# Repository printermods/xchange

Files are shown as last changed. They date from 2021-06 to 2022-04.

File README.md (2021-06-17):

# XChange
XChange printable adapters, firmware, knowledge base, accessories
(This repository will be updated frequently as we further develop adapters, installation and operation support materials, and more. Please contact us directly for general one-on-one help at support@printermods.com)

======================================================

# Start Here
Read and watch the following before beginning installation of your XChange:

#1 - XChange V1.0 - Basic Installation Instructions: https://www.youtube.com/watch?v=RV0KnSQEELk

#2 - Warnings and Pre-Installation Checklist: https://github.com/printermods/xchange/blob/main/XChange%20V1.0%20-%20Pre-Installation%20Checklist%20Rev%200.pdf

#3 - Wiring Notes and Diagrams: https://github.com/printermods/xchange/blob/main/XChange%20V1.0%20-%20Wiring%20Diagrams.pdf

#4 - Measuring and Calculating Belt Length: https://github.com/printermods/xchange/blob/main/XChange%20V1.0%20-%20Belt%20Lengths.pdf

#5 - Frequently Asked Questions: https://github.com/printermods/xchange/blob/main/FAQ

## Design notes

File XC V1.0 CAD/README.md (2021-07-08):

As we release CAD files for XChange, they will be organized and updated here.

*All works herein published under the Creative Commons Attribution-NonCommercial 4.0 International license: https://github.com/printermods/xchange/blob/main/LICENSE.txt *

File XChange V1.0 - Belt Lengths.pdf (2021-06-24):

# XChange V1.0 - Belt Lengths

## How to Determine if You Need a Different Belt

You may need to replace your X axis drive belt in order to use XChange on your 3D printer, if the belt tabs on XChange are significantly longer or shorter than the ones currently in use on your machine.

Below is a chart of the belts that we’ve personally tested on some popular machines. Note that lengths in this chart represent the belt length between the ferrules (terminations). We’ll update it as we confirm new lengths, and receive input from you!

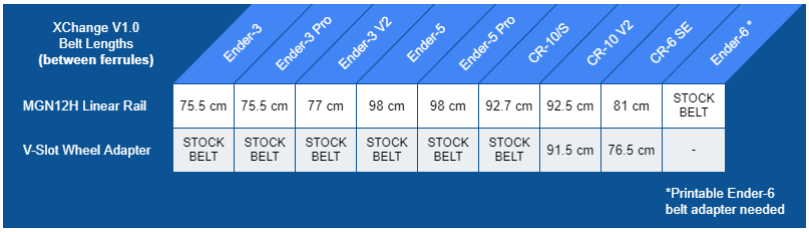
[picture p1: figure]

Measuring Custom Belt Length
If you don’t see your printer listed above, don’t worry, there are a couple of options. The simplest is to just install XChange, and cut a piece of belt to the appropriate length. You can terminate the ends by folding the end of the belt over itself to make a loop, then securely fastening with zip ties:

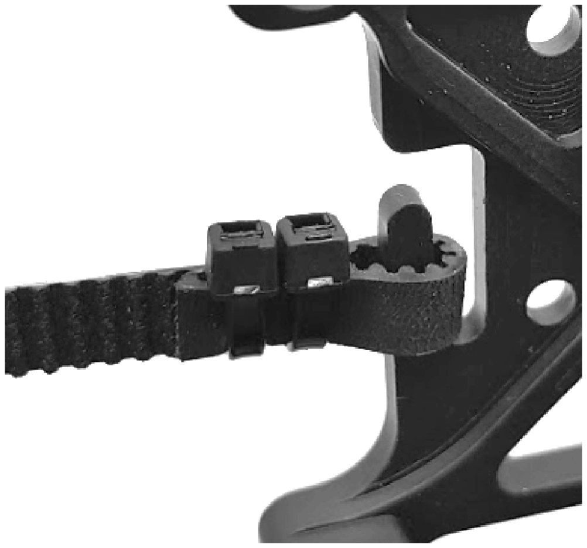
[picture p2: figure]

## XChange V1.0 - Belt Lengths

Belt Length Calculator
You can alternatively use our spreadsheet to measure and calculate the specific length you’ll need for your installation, depending on your X axis linear motion. If you provide this information to us at the time of placing your order, we can custom cut and pre-terminate a high quality belt for you.

Note: Belt length calculator spreadsheet is downloadable, and .XLSX format. You can upload to and open in a free Google Drive account if you don’t have Microsoft Excel:

https://drive.google.com/file/d/1cvCTFK-Esp-tSwJrwVX8-UBtqmJn4-DE/view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 (https://drive.google.com/file/d/1cvCTFK-Esp-tSwJrwVX8-UBtqmJn4-DE/view)

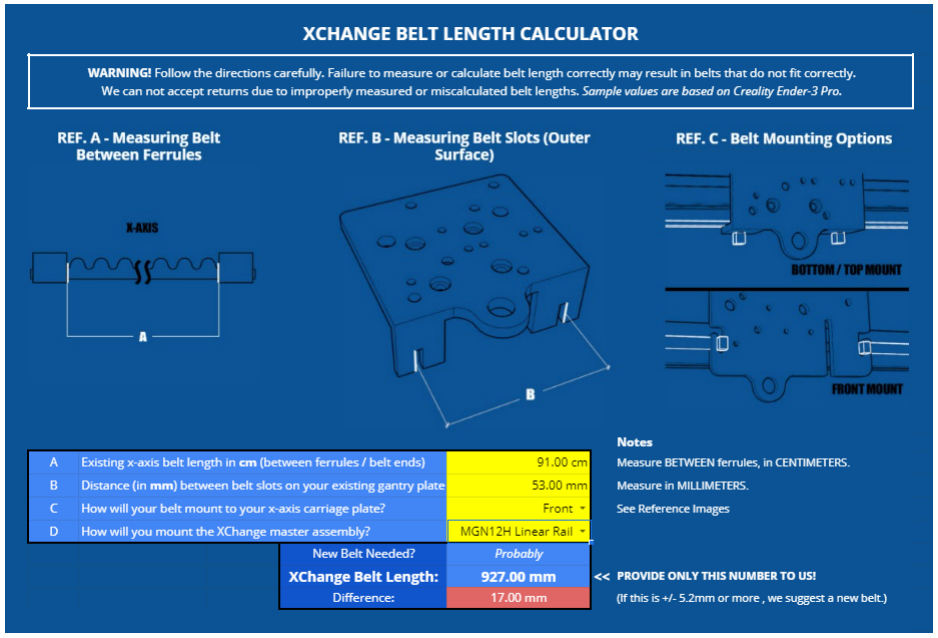
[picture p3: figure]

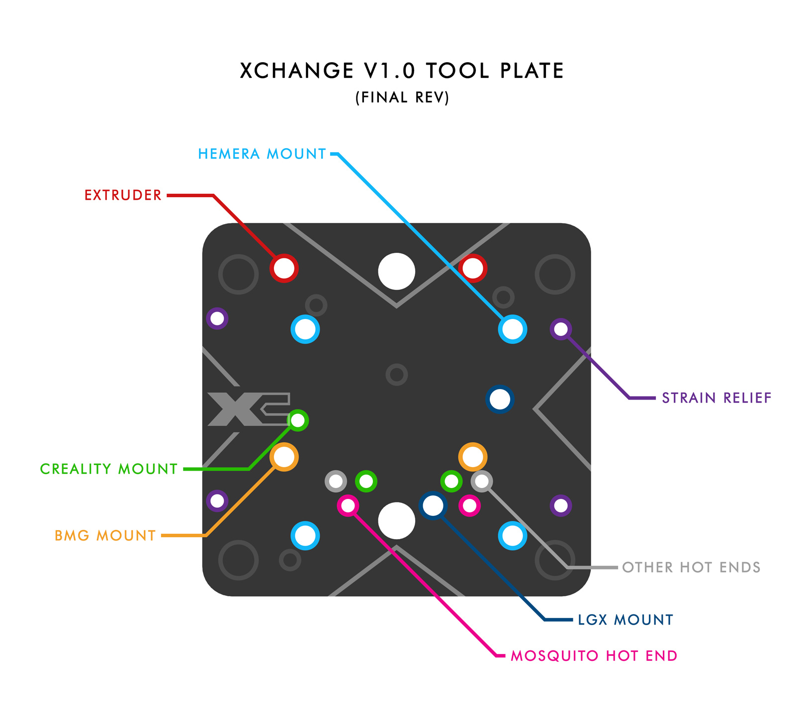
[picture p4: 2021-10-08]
XChange-v1-tool-plate-diagram.jpg

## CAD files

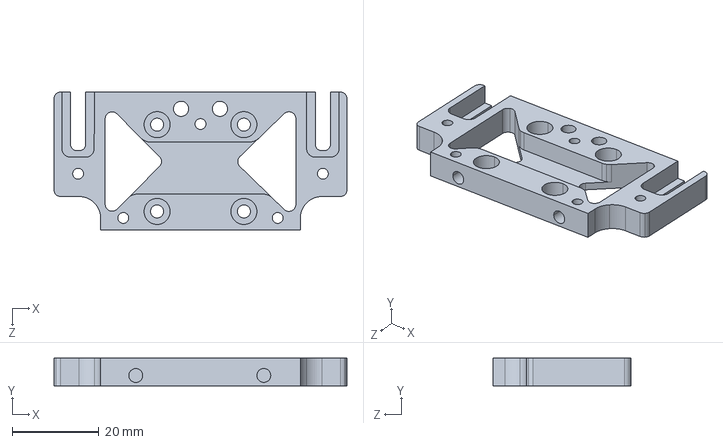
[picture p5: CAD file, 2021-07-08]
XC V1.0 CAD/STEP/Master-Assembly-M2-V9.step
67.5 x 6.35 x 31.8 mm

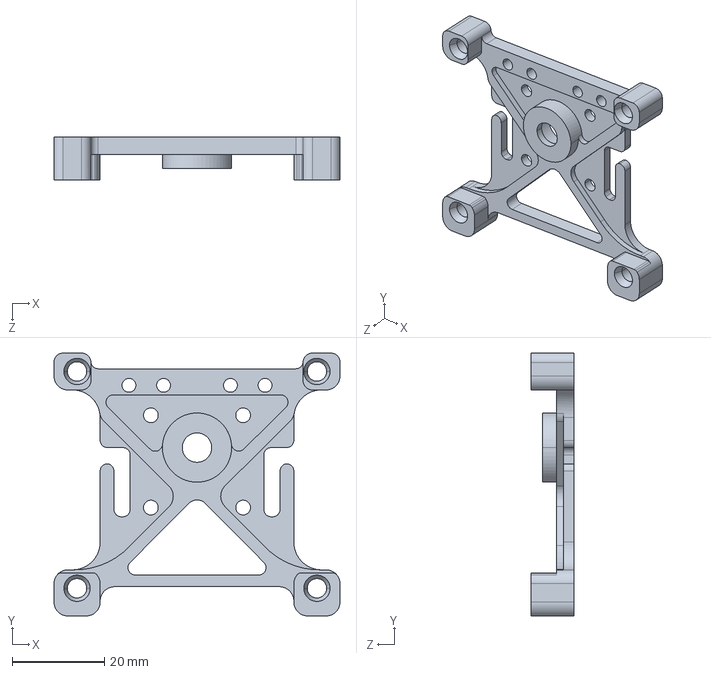
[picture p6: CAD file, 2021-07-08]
XC V1.0 CAD/STEP/Master-Assembly-M1-V13.step
62.0 x 57.0 x 9.30 mm

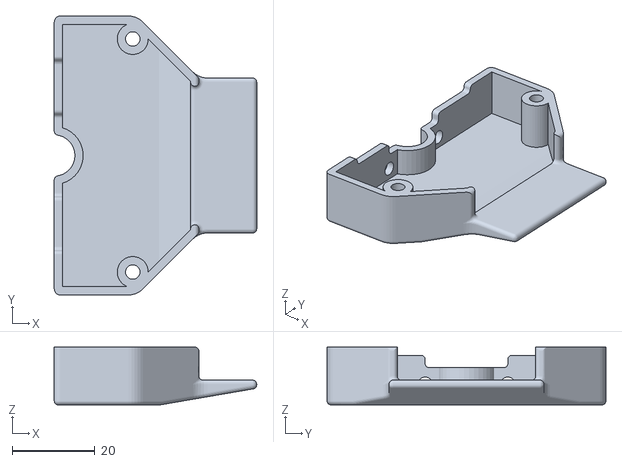
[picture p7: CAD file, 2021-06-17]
Printable Files/Master Assembly Cover - TT.stl
49.0 x 67.5 x 14.0

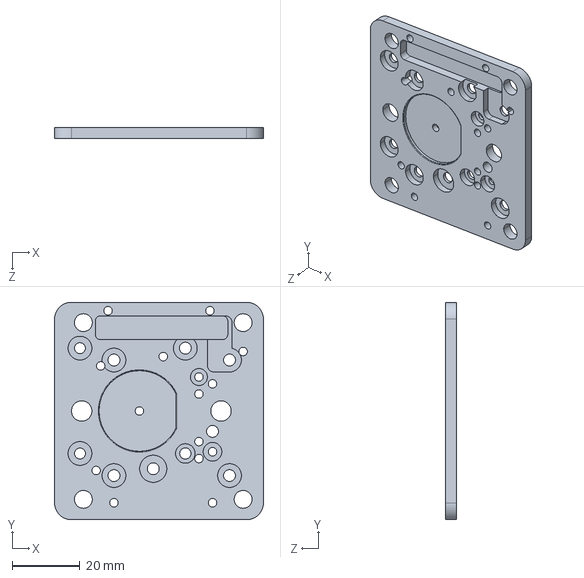
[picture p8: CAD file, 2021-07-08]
XC V1.0 CAD/STEP/Tool-Assembly-Plate-V2.step
61.5 x 64.0 x 3.18 mm

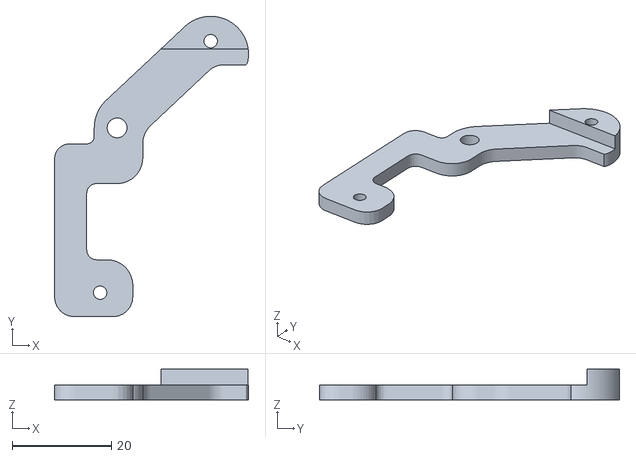
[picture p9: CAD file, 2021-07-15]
Printable Files/ender-stock-fan-shroud-xchange-v2.stl
39.1 x 60.6 x 6.18

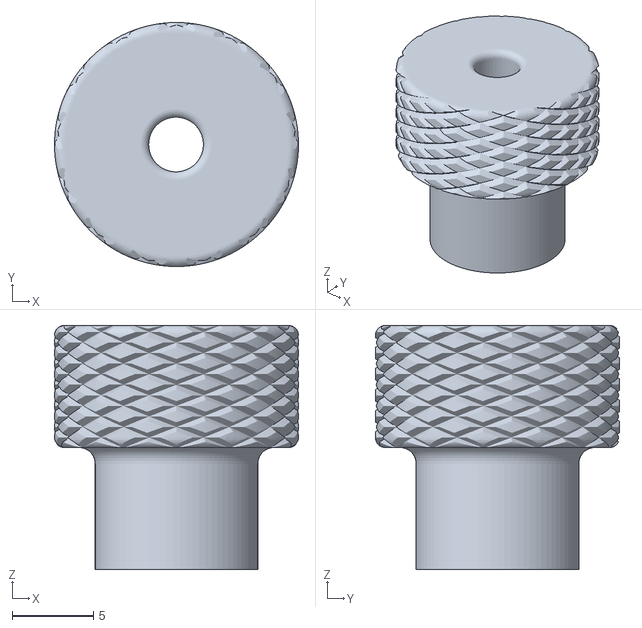
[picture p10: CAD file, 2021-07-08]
Printable Files/alignment-tool-v2.stl
15.0 x 15.0 x 15.0

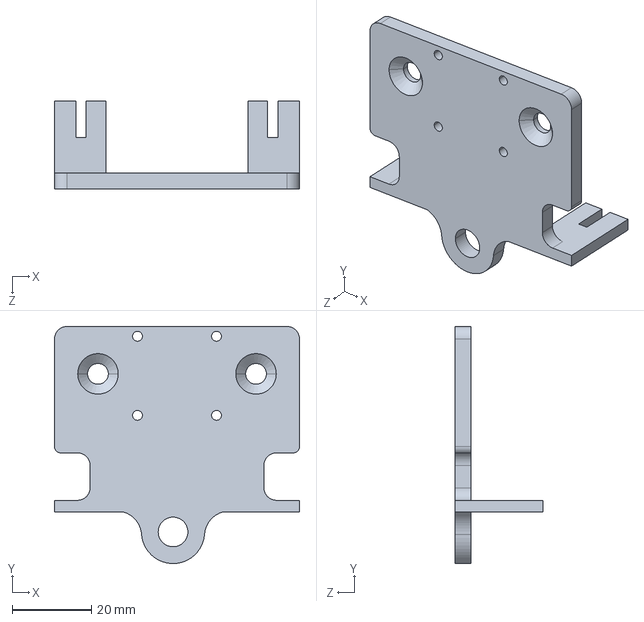
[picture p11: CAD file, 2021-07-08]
XC V1.0 CAD/STEP/E3-V-Slot-Adapter.step
62.0 x 60.0 x 22.2 mm

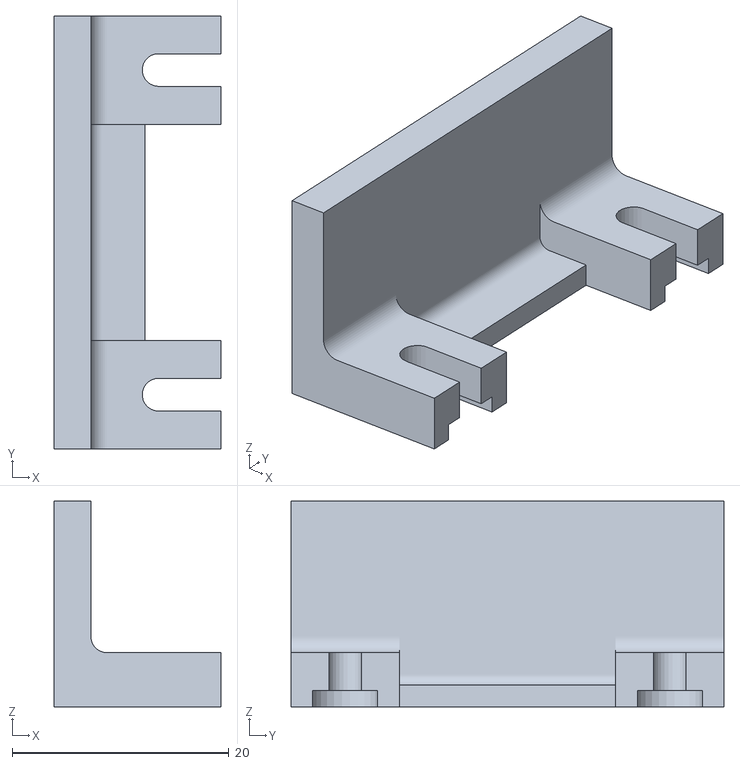
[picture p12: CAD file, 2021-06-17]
Printable Files/tool-plate-wire-cover.stl
15.4 x 40.0 x 19.0

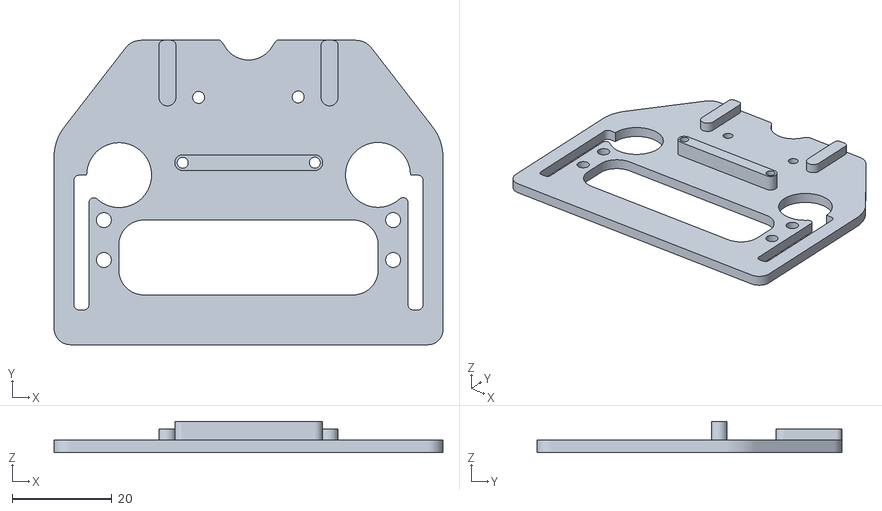
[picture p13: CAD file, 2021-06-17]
Printable Files/Ender 6 Printable Belt Adapter v4.stl
78.0 x 61.1 x 6.30

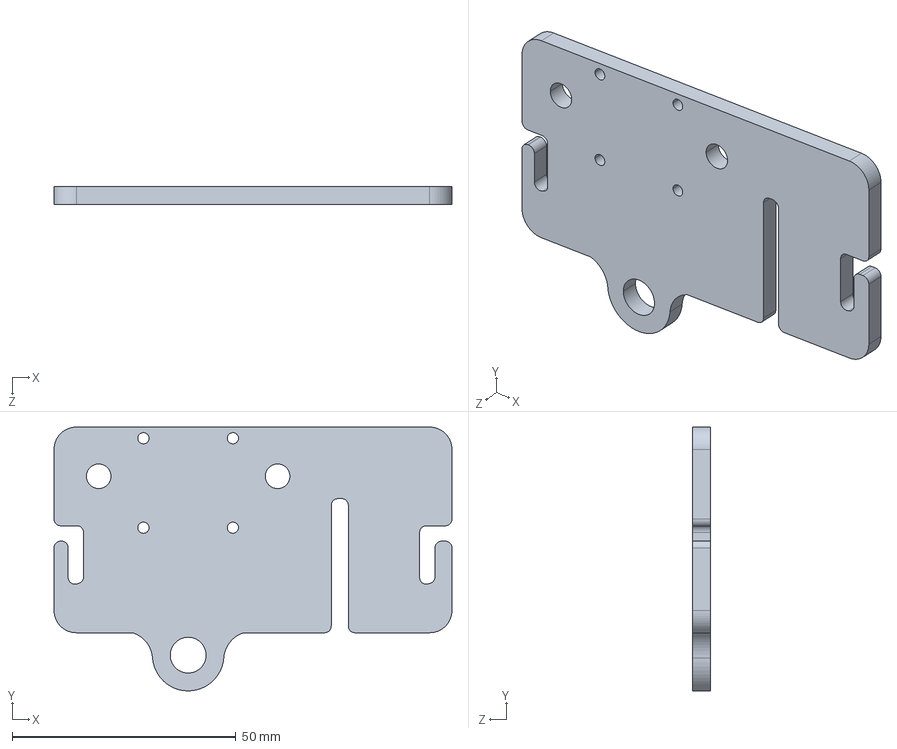
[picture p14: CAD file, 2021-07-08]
XC V1.0 CAD/STEP/E5-V-Slot-Adapter.step
89.0 x 59.0 x 4.00 mm

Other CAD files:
XC V1.0 CAD/STL/M2-v9.stl
XC V1.0 CAD/STL/M1-v13.stl
XC V1.0 CAD/STL/E3-V-Slot-Adapter.stl
XC V1.0 CAD/STL/E5-V-Slot-Adapter.stl
XC V1.0 CAD/STL/Tool-Assembly-Plate-V2.stl

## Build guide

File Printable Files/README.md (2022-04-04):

**Have a print you'd like us to share? Send it to us, along with a description, at support@printermods.com and we'll check it out!**

**Alignment Pin Tightening Tool:**
https://github.com/printermods/xchange/blob/main/Printable%20Files/alignment-tool-v2.stl

**Ender-6 Printable CoreXY Belt Adapter:**
https://github.com/printermods/xchange/blob/main/Printable%20Files/Ender%206%20Printable%20Belt%20Adapter%20v4.stl  

**Ender-3 / Ender-5 / CR-10 Style Fan Cover Adapter:**
https://github.com/printermods/xchange/blob/main/Printable%20Files/ender-stock-fan-shroud-xchange-v2.stl

**Tool Plate Wire Cover:**
https://github.com/printermods/xchange/blob/main/Printable%20Files/tool-plate-wire-cover.stl  

**Master Assembly Cover (90º wire strain relief)**
https://github.com/printermods/xchange/blob/main/Printable%20Files/Master%20Assembly%20Cover%20-%20TT.stl  
*Design credit: Teaching Tech*

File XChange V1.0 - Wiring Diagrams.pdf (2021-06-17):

# XChange V1.0 - Wiring Notes and Diagrams

## Wiring XChange Master and Tool Assemblies

Wiring your Master and Tool Assemblies is actually quite simple, and wiring is 1:1 between the Master PCB and Tool PCBs. This means that whatever circuit you wire to the “HF+” connector on the Master PCB will correspond exactly to the “HF+” connector on the tool PCB.

ONLY wire your heater cartridge to the connections labeled “+” and “-”, as these are connections with thicker board traces specifically for higher wattage components.

For installations requiring a more advanced understanding of XChange’s circuit paths, please refer to the schematics at the end of this document.

## XChange V1.0 - PCB Wiring Diagrams

Master PCB Drawing

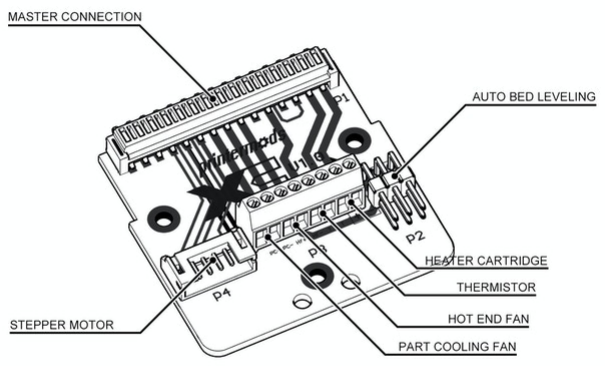
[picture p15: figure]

## XChange V1.0 - PCB Wiring Diagrams

Tool PCB Drawing

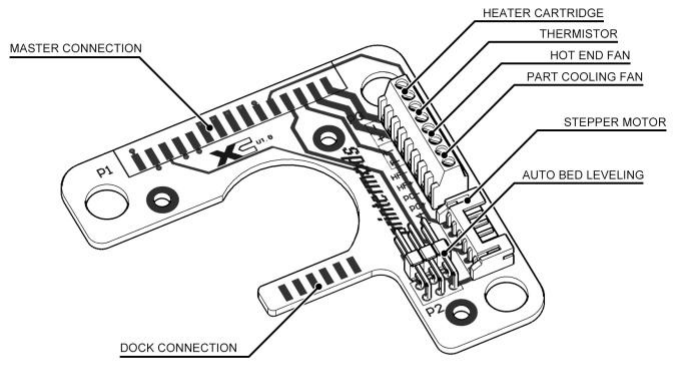
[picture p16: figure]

## XChange V1.0 - PCB Wiring Diagrams

### (MASTER PCB SCHEMATIC)

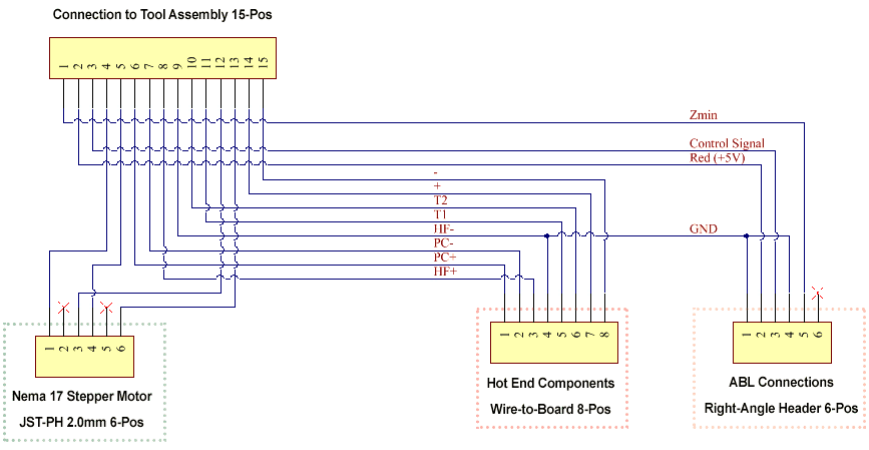
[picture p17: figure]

## XChange V1.0 - PCB Wiring Diagrams

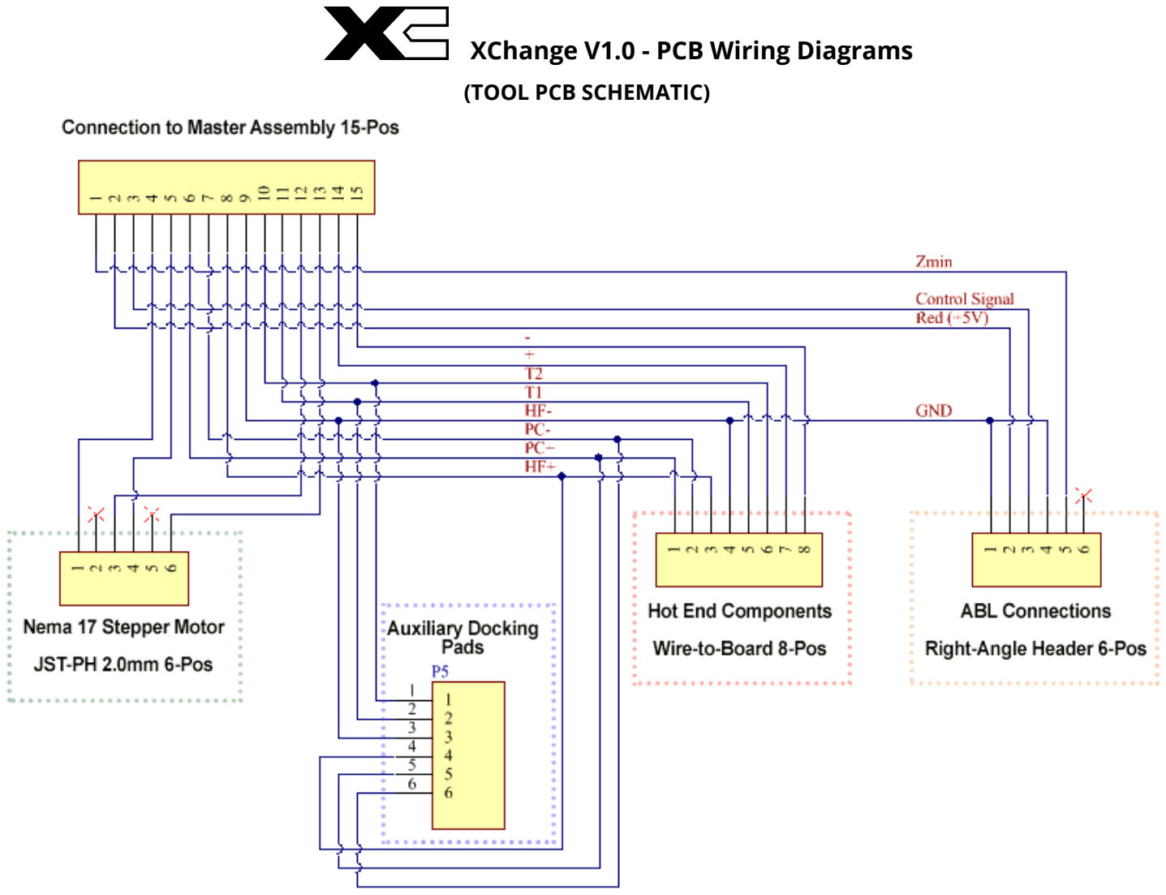
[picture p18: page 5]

### (TOOL PCB SCHEMATIC)

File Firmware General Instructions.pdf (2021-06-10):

The most current firmware solution for XChange is Marlin-bugfix-2.0.x, which has had revisions made by a Marlin firmware dev now merged into the official branch. The primary change is the ability to define M206 offsets while using Marlin’s tool change functionality.

Tool presets are stored on the “auto0.g” file, which should be loaded to the printer’s SD card (card should be inserted prior to powering the printer on).

The format for tool head configuration in auto0.g is as follows:

M810 M206 X0Y0Z0 | M92 E93 | M301 P21.3I1.54D76.55 | M204 P500 R500 T500
| M900 K0.0 | M305 R4700 T100000 B4092; Stock Head

M81X - Tool number
M206 - Toolhead offset relative to zero
M92 - E-step calibration
M301 - PID calibration
M204 - Acceleration values
M900 - Linear Advance settings
M305 - Thermistor parameters

Please exercise caution when using this experimental firmware and tool changing configuration files. Be especially careful when attempting bed leveling, and ensure that Z safe homing is enabled. It is recommended to use only manual mesh bed leveling with XChange for now.

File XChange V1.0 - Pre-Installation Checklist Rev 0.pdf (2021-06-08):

# XChange V1.0 - Pre-Installation Checklist

# WARNING!

This device is not a toy. If you are not knowledgeable about 3D printer electronics, please consult an electrical professional for help with installation. Always service your XChange-equipped 3D printer with the power OFF, as its magnets are capable of attracting metallic tools and objects with significant force. The magnetic locking system poses a pinching hazard, and may cause injury if misused. If misused or installed incorrectly, or used without supervision, this device may damage your 3D printer and other electronics. We are not liable for damage arising from the use or misuse of this device.

## Before you begin…

XChange is the first system of its kind, and you are one of the first with access to it! While this system was generally designed for compatibility with most 3D printers, there are MANY variables that impact compatibility with different machines and accessories. Before converting your machine to use XChange, it’s important that you take your time, think carefully about all the steps, and print or purchase anything you’ll need that you don’t already have. Please watch any and all instructional videos ahead of time to understand any hurdles you may encounter.

We’ll be working to ensure compatibility for as many machines as we can, and this process will be heavily dependent on design input and contributions made by the community. We appreciate your patience during this process, and ask that you refer to github.com/printermods/xchange to find helpful documentation, files, and share with the community.

## 1. Plan your build!

”Measure twice and cut once.” Gather all printable files you’ll need, and identify any parts you’ll need to design, find or purchase. Think about belts, endstops, coordinate changes, firmware adjustments, etc. Then, start by getting your machine printing perfectly with a single tool before moving to assembling the next one. Use our support channels and growing knowledge base for answers to your general installation and usage questions.

Find our downloads and knowledge base at github.com/printermods/xchange

2. Use support resources (and contribute, if you’d like).
XChange’s Kickstarter campaign has granted backers early access to pre-release offerings.

XChange V1.0 Pre-Installation Checklist - Rev. 0

As XChange has not yet been commercially released, it may require adaptation to suit your specific printer model-- adaptation that we may or may not yet have developed or vetted. The feedback and ideas you provide helps us make XChange even better and broadly compatible as we move forward. Be sure to check all documentation, warnings, and requirements before installing XChange.

3. Be careful.
We recommend installing XChange on secondary or non-critical machines until you are completely familiar with its installation, maintenance, and usage. You can avoid costly mistakes by following common sense guidelines such as:
- Print the appropriate master assembly strain relief adapter, and ensure all connections have proper strain relief.
- Print and attach the master assembly safety shroud (never use XChange without this part in place).
- Only service your machine with the power OFF.
- Never place your fingers or any other objects between the magnetic assemblies.
- The magnets are strong enough to grab tools such as screwdriver and hex key bits, so use caution when working in close proximity to them.
- Take care to correctly align tool plates as they are attached to the master assembly.
- Do not drop tool assembly, as pins can break and components may be damaged.
- Take care to leave no stray wires when inserting stripped ends into wire-to-board connectors.
- Additional mechanical reinforcement may be necessary when using tool plate accessories in excess of 600g.
- Do not exceed the rated safe electrical limitations of the PCBs of 2.8A per pin.

## 4. Have fun!

Perhaps most importantly, we hope XChange sparks new ideas and creative ways for you to use your 3D printer. We’d really love to hear from you, and encourage you to share your successes— and failures— with us. Our team has worked tirelessly to provide you something we hope you’ll really love, and sharing those experiences with us is very meaningful to everyone. Reach out to us directly at support@printermods.com .

We sincerely thank you for being our backer, and making XChange possible. <3

XChange V1.0 Pre-Installation Checklist - Rev. 0

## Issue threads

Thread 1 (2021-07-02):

Couple questions

zcohenld, 2021-07-02:
I received my XChange today and have been playing with it a bit. Haven't mounted anything yet since I'm still figuring out how I'm going to do everything. A few things have come up though that I wanted to ask/bring up for others.

- The installation guide video needs some work. The sound is pretty bad and sometimes its hard to see whats actually being done. I dont expect it any time soon, but I feel videos in general just aren't the best way to show how to assemble something. I found the [Inventables X-Carve instructions](https://x-carve-instructions.inventables.com/1000mm/) to be extremely well done. Something like that would be really helpful.
- It would be helpful to see installations on multiple printers and not just a CoreXY. Specifically seeing the setup on a bed slinger would be really helpful since I feel like a lot of people have that style of printer.
- In the video you mentioned a 3D printable tool to install the alignment pins. Do you have a link to that?
- It would be nice to have pictures of the various mounts that you have as STLs on GitHub. I've been looking at figuring out how to mount the Petsfang system I use for everything and saw the ender stock fan shroud adapter. I think that works, but when I loaded it into CAD with the plate I couldn't quite figure out how it was mounted exactly. Having a picture of it mounted to a tool plate for that and any other mods would be super helpful.
- You had mentioned it in an email, but we really need a community to discuss with each other. Anything, be it Slack, Discord, Facebook, whatever. It would be nice to ask others who are using this system and not be out there on my own figuring it out. Also as I figure things out I want to contribute, but dont really know where to do so yet.
- For the actual XChange, everything seems well made/machined except for the anodization. I ordered five tool plates and a master assembly and all of them came out of the bag with scratches. Personally I don't care and am not looking for anything to fix it for me, but it doesn't look great receiving something with scratches.
- The packaging overall was simple but does there have to be so many bags? I'm throwing out a ton of single use plastic bags and its kind of depressing. I dont think every type of part needs its own bag. Or if there does need to be separation, at least a more environmentally friendly way would be nice.

Thanks overall for a pretty awesome looking product. I'm looking forward to installing it!

zcohenld, 2021-07-02:
Sorry, one more question. What is the purpose of the auxiliary docking pads on the tool plate side?

scepterr, 2021-07-03:
There's a Facebook group available, https://www.facebook.com/groups/549481366050754

printermods, 2021-07-06:
@zcohenld Great questions / feedback, thank you. See our replies in order:

- We are definitely creating a web-based and PDF guide for installation! The video was really intended to be a band-aid for the near term, and we apologize that the quality isn't up to snuff. Future videos will be much better.
- The Ender-5 was chosen as kind of a middle-ground machine, but we plan to do publish our instructions for an Ender-3 V2 machine, which should be a little more universal (and simpler).
- That alignment pin tool will be published today in the Printable Files section.
- As @scepterr mentioned, the Facebook group is the one we've landed on right now based on user feedback. We'll also try to be responsive to comments and issues here as well.
- Would you send us photos of the anodization issue you had? We'd like to see if the scratches you're referring to occurred post-anodization, as we had a batch from our anodize partner packaged a bit haphazardly and that's a possibility. If you'd be so kind, please send them to us at support@printermods.com and reference this conversation.
- You're absolutely right about the packaging. We planned on having custom-cut foam inserts ready by now, but worldwide PU foam shortages have necessitated that we put that plan on hold. We're working on a solution that will be more environmentally friendly, easier to unpackage, and easier for us to package as well.

Thanks for taking the time to give your feedback!

printermods, 2021-07-09:
> Sorry, one more question. What is the purpose of the auxiliary docking pads on the tool plate side?

Sorry we missed this. The auxiliary docking pads on the tool boards are for a secondary, powered "stand by" dock that we will be releasing plans and kits for. It will include auxiliary connections for powering the heater, hot end cooling fan and thermistor for each tool, with the intention of bringing that tool to (and sustaining) a desired temperature while not connected to the master assembly.

zcohenld, 2021-07-11:
That's so extremely cool and such an awesome idea. Thank you for sharing! I'm really excited to see that!

Closed 2021-07-06.

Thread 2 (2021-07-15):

stock fans

bakaneko718, 2021-07-15:
i see there is a file here for stock fan shroud, but i cant download it to check it out and see how it will work for me. there are a few of the files that are not available to download actually.

somewhat related is there a scale diagram for the tool plate?

printermods, 2021-07-15:
Thank you for bringing this to our attention.

To the best of our reckoning, it's a GitHub issue, and we've created a ticket and asked for their help.

We will leave this issue open until it's resolved. In the meantime, two options:  you can either download the raw data and save it to a notepad file (rename it X.STL), or you can download the entire repository from the home directory.

Sorry for the inconvenience.

printermods, 2021-07-15:
@bakaneko718 oops, turned out to be an export / encoding issue with the file upon closer inspection. It's corrected now. Thanks!

Closed 2021-07-15.

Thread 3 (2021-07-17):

Release STEP files for missing parts please

evilC, 2021-07-17:
Please release STEP files for the lever arm, the locating pins, and the PCBs

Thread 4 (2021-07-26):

Stock fan shroud

bakaneko718, 2021-07-26:
There is a file of a bracket for the stock fan shroud on the ender 3 pro, but it doesnt account for the direct drive set up nor does there seem to be a clear way to attach it to the tool plate. I am using the direct drive set up that I had purchased from your store.

Next-victim, 2021-11-12:
I straight up mounted my MDD carage plate to the Xchange to get mine going. Not great, but doesnt seem to interfere with anything. Here's a phone from the mounting test, before rewirin
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

I don't know what else to call it but pure jank. Only the 2 hotend screws and the SINGLE screw to the right of them actually line up, so I back fead the one that wasnt part of the hotend. Then used a small screw as a guide for the left one and got the right screw passed througth the hot end and both plates. From there, I got the left hot end screw in by fiddling with it and not removing the far right "alignment" screw. I then proceeded to remove the alignment screw and back feed it with a small screw that wouldnt hit the hot end or interfere with the XChange setup.

My off sets are screwed but it will let me print a front plate brackate with opening for the Ender 3 fan assembly. This is on an Ender 5 but the idea is the same for the 3 and 5, just a narrower bracket on the 3.
g.

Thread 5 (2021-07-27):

Tool plate wire cover missing some PCB cutouts

evansj, 2021-07-27:
The tool plate wire cover has a cutout to clear the PCB around where the cable attaches, but cutouts are missing from the sides (just in front of the mounting bolt holes). It means that the cover can't sit flat on the top plate.

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

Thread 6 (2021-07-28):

Hole pattern diagram for the XChange Tool Plate

C0unt23r0, 2021-07-28:
I've seen a description for each hole on your homepage for the MDD tool plate but not for the XChange.
Link: https://cdn.shopify.com/s/files/1/0054/6311/3799/products/MDD-V1.3-ENDER-3-CR-10-DIRECT-DRIVE-HOLE-PATTERN-DIAGRAM_a29303f0-6256-46aa-8563-0ae83a8569ad_495x495.png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

Would be nice to see for what all these holes are meant for. I hope I didn't missed anything.

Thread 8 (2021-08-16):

Feature: Enabling XChange to be mountable on the bottom side of the x-axis

C0unt23r0, 2021-08-16:
Thinking about cable management and holding XChange in my hands i had an idea. What if it would be possible to turn everything except the tool plate by 180 degree. That would enable it to put a cable chain lying on top of the x-axis like the Voron is designed for.

Technically the only part that has to be change would be the pcb on the toolplat and the mounting holes for the screes that are restricting the possibility. Maybe in Version >2?

My workaround for now is use an adaptor between the tool plate and the print head

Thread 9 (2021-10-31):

Request: make it easier to mount things on the rear

Phantom329, 2021-10-31:
I would like to request that in the updated version of the master top plate to make it easier to mount things to the rear. Maybe add 2 or 3 tapped holes on the back edge.

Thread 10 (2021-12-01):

Community Discord or Discussions on Github?

joshstortz, 2021-12-01:
I have recently installed the XChange system on my Ender 3, but have struggled with the firmware changes to ensure the nozzle/probe positions doesn't flag the Marlin sanity checks.  I've essentially had to change the bed size from (235,235) to (201,194) with the HeroMe Gen5 and want to see if I can gain some of that space back.

Is there a plan or timeline you can provide on when a Discord server or discussion group will be available?  I see some posts of interest on the Facebook group, which I just joined, but I'm not a fan of FB's interface for having in-depth discussions.

Thanks in advance.

x-Rune, 2022-01-21:
I would like to join a community Discord as well, since I no longer use FB at all. If we don't get an officially supported one, I will create one if there is enough interest.

Flapstaart, 2022-03-24:
> I would like to join a community Discord as well, since I no longer use FB at all. If we don't get an officially supported one, I will create one if there is enough interest.

I would be happy to join. I truly don't understand why a choice was made for a closed FB group. This would sooner force me to sell my Xchange kit than have me create a FB account.

V1tamnT, 2022-04-01:
I'd join a Discord to not have to use FB.

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

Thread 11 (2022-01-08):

Auto bed leveling connector

RJSavell, 2022-01-08:
It does not appear that pin 4 on the auto bed leveling connector is connected to the ground (or pin1) as shown in the schematics.   Is this pin not needed for the BL Touch / CR Touch or are we supposed to solder a wire between these pins?

zchrykng, 2022-01-18:
I just went through a checked the connections with a multi-meter. One of the pins is actually completely dead. I’d just go through and check it personally. Two of the pins are connected to a common ground, so make sure you don’t hook your 5v to one of those for instance.

RJSavell, 2022-01-19:
I have checked every pin on P2 and P2 pin 6 is marked a NC so that is expected but P2 pin 4 should go to P1 pin 9 (ground) but it is not  connected to anything, I checked all of the possible connection.   This is the same on the 3 tool plate PCBs and the master PCB.  I have a friend who bought this at the same time as I did and he has the same problem.

zchrykng, 2022-01-19:
Take a look at the image in this pull request. The pins are labeled. https://github.com/printermods/xchange/pull/7/files

zchrykng, 2022-01-19:
Maybe you got a bad unit then. I’ve verified that what I said is the case on what I have.

RJSavell, 2022-01-20:
as it turns out I had pins 4 and 6 reversed - while I swore I had tested every combination apparently I has not :-(
Thanks for everyone help!!!

Closed 2022-01-20.

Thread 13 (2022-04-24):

ABL wiring diagram for BL Touch

jackrod, 2022-04-24:
Is there a color code spec anywhere I can refer to? I just want to hook up my BL Touch to the 6 pin ABL connection on the board. Any recommendations on what type of connector I can use for the 6 pin?

Thanks,
Jack

TwinkieXLII, 2022-05-03:
I see one pin has a square pad, not sure if that's pin 1 or pin 6.

sogeniusio, 2022-05-03:
Check out the posts on the Fb page. https://www.facebook.com/groups/549481366050754/search/?q=bl-touch

sogeniusio, 2022-05-03:
I made this diagram, which helps me. But from others on the Fb group are saying it may be wrong. I would check for continuity before plugging anything in. I killed a few bl-touch during trial and error.

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

griffout, 2022-12-25:
I know this is an older post, Just wondering if you fried your BLTouch or if this worked for you?
